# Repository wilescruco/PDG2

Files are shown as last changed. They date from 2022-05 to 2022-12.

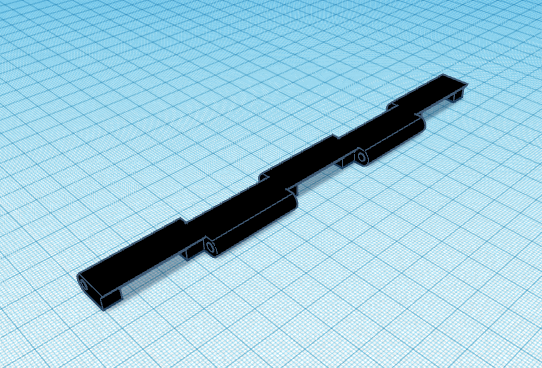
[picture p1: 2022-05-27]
DISEÑOS DE CONSTRUCCIÓN/Diseños de las Piezas impresas en 3D Banda/Pieza Banda.png

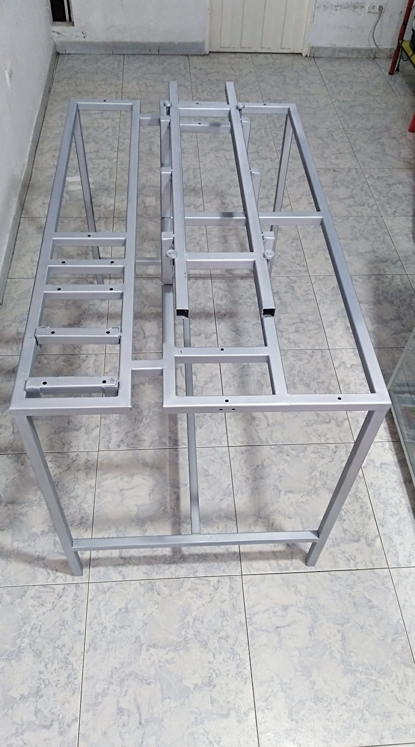
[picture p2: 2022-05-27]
DISEÑOS DE CONSTRUCCIÓN/FOTOS MESA BANDA TRANSPORTADORA/2. ESTRUCTURA METALICA.jpg

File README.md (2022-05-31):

# PDG2
BANCO PARA PRÁCTICAS DE AUTOMATIZACIÓN INDUSTRIAL, CONTROL AUTOMÁTICO DE UNA BANDA TRANSPORTADORA MEDIANTE UN VARIADOR DE FRECUENCIA CON PLC

Completa

Mecanismo interno

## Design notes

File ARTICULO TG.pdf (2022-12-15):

# BANCO PARA PRÁCTICAS DE AUTOMATIZACIÓN INDUSTRIAL, CONTROL AUTOMÁTICO DE UNA BANDA TRANSPORTADORA MEDIANTE UN VARIADOR DE FRECUENCIA CON PLC

Wilson Sneider Cruces, Paola Andrea Ovalle

Fundación Universitaria Unisangil

wilsoncruces@unisangil.edu.co

paolaovalle@unisangil.edu.co

Resumen— El siguiente articulo contiene el desarrollo del diseño e implementación de un banco para prácticas de automatización aplicando control automático a una banda transportadora mediante un variador de frecuencia controlado por PLC, este proyecto además de su estructura física, cuenta con guías de laboratorio, manual de usuario y planos eléctricos que le permitirá a los estudiantes de la Fundación Universitaria Unisangil sede Yopal, interactuar y poner en práctica los conocimientos teóricos adquiridos en las diferentes áreas de la ingeniería tales como instrumentación industrial, maquinas rotativas, programación, control y automatización de procesos, mediante el desarrollo de prácticas de laboratorio.

Abstrac— The next document contains the development of the design and implementation of a bench for automation practices applying automatic control to a conveyor belt through a frequency inverter controlled by PLC, this project, in addition to its physical structure, has laboratory guides, a user manual and electrical plans that will allow the students of the Yopal Unisangil University Foundation to interact and put into practice the theoretical knowledge acquired in the different areas of engineering such as industrial instrumentation, rotating machines, programming, control and process automation, through the development of laboratory practices.

I. INTRODUCCIÓN
GSL industrias define la automatización industrial como el uso de sistemas computarizados, electromecánicos, electroneumáticos y electrohidráulicos para fines industriales. Dentro de las ramas de ingeniería, es uno de los procesos más completos y transversales a diferentes actividades industriales a nivel nacional. [1]

El presente articulo da a conocer el proceso de diseño e implementación de banco para prácticas de automatización aplicando control automático a una banda transportadora mediante un variador de frecuencia controlado a través de un PLC, con el objetivo de que en un futuro permita a estudiantes de carreras universitarias afines, desarrollar sus prácticas en las áreas de instrumentación industrial, maquinas rotativas, programación, control y automatización de procesos, quedará disponible para que los profesionales en formación puedan valerse de él para afianzar sus conocimientos, además, servirá de base para futuras mejoras o innovaciones.

II. PLANTEAMIENTO DEL PROBLEMA

En Colombia según datos de Asocoldep la ingeniería Electrónica está dentro de las carreras mejor pagadas y con mayor demanda en vinculación laboral con un promedio del 84.4%. Convirtiéndola en una buena opción de formación profesional. La accesibilidad a estas carreras universitarias es relativamente fácil, además hay un número considerable de universidades que ofrecen diferentes programas profesionales de ingenierías, estando al alcance de cualquier joven con aspiraciones de aprendizaje en estas áreas. Dentro de estas entidades de formación existe una problemática, que interfiere en el proceso de formación de estos profesionales y se trata de la falta de espacios adecuados y laboratorios que les permita a los ingenieros electrónicos en
formación | desarrollar | sus | conocimientos, | aplicarlos | y
relacionarlos en los campos de la instrumentación industrial,
electrónica | de | potencia, | diseño | electrónico, | control | y
automatización. [2]

La Fundación Universitaria de San Gil UNISANGIL sede Yopal que cuenta con un amplio grupo de jóvenes con grandes inspiraciones de aprendizaje, encaminados en un proceso de formación en diferentes facultades de las ingenierías, una de ellas la ingeniería electrónica. Esta ingeniería es una carrera profesional con bastante exigencia como cualquier otra, su etapa de teoría como la práctica, son muy importantes a la hora de pensar en ser un excelente profesional. Teniendo en cuenta lo anterior la sede UNISANGIL Yopal viene trabajando en fortalecer sus espacios de laboratorio de tal manera que les brinde a sus estudiantes un ambiente de aprendizaje apropiado dotado con recursos que permita realizar las prácticas de laboratorio, espacio esencial para el proceso de formación profesional.

III. FORMULACIÓN DEL PROBLEMA.

¿ La construcción de un banco para prácticas de automatización industrial, control automático de una banda transportadora mediante un variador de frecuencia con PLC, ayudará a los estudiantes de ingeniería electrónica a mejorar sus habilidades en el desarrollo de prácticas de programación de PLC y automatización?

IV. JUSTIFICACIÓN.

Una de las principales áreas de desempeño de un ingeniero electrónico es la automatización y control de procesos; los procesos automatizados en la actualidad tienen una alta demanda ya que el diseño de estos sistemas van enfocados al mejoramiento y optimización del mismo, teniendo en cuenta lo anterior, se considera de vital importancia que la Fundación Universitaria de San Gil Unisangil cuente con espacios de laboratorios adecuados que les permita a los ingenieros en formación interactuar con equipos, sistemas y tecnologías implementadas en áreas de Instrumentación, control y automatización, tales como el controlador lógico programable.

Pensando en la calidad de formación del ingeniero electrónico, la Fundación Universitaria Unisangil sede Yopal ha venido mejorando los espacios laboratorio de electrónica, hasta el momento varios estudiantes que están finalizando su proceso de formación, como trabajo de grado, han desarrollado e implementado diferentes bancos de prácticas; con el fin de seguir contribuyendo con la adecuación y equipamiento de esta área tan importante el en proceso de formación de los ingenieros electrónicos, nace la idea de diseñar un banco para prácticas de automatización industrial, en este caso, el control automático de una banda transportadora mediante un variador de frecuencia con PLC. Este nuevo banco para practicas quedará al servicio del laboratorio de la universidad y para uso de todos los estudiantes del programa de ingeniería electrónica, de esta manera la Fundación Universitaria de San Gil UNISANGIL mejorará tanto su laboratorio como la calidad de formación que ofrece a sus profesionales.

V. OBJETIVOS
A. Objetivo general.

Diseñar e implementar un banco para prácticas de automatización aplicando control automático a una banda transportadora mediante un variador de frecuencia con PLC.

B. Objetivos específicos
- Desarrollar la plataforma de trabajo de la banda transportadora.
- Diseñar y realizar la estructura del banco de prácticas, donde se integre la banda transportadora y el motor junto con su control automático
- Desarrollar el programa para el controlador lógico programable que permita la automatización del proceso mediante el variador de frecuencia.
- Realizar pruebas de funcionalidad del sistema para verificar su correcto funcionamiento y de esta manera alcanzar el objetivo principal del proyecto.
- Diseñar cuatro guías de laboratorio que les permita a los estudiantes interactuar con el banco de prácticas y conocer cada uno de los sistemas que lo componen.

VI. ESTADO DEL ARTE.

En la fundación universitaria Unisangil sede Yopal, los Ingenieros en formación le han apostado a contribuir con el equipamiento de los espacios de laboratorio de la ingeniería, con el desarrollo e implementación de bancos para prácticas de neumática, electro neumático, modulo variador de frecuencia, banco de procesos industriales, entre otros, estos proyectos, además de permitirle a los ingenieros en formación aplicar sus conocimientos con ejecución de estos, también contribuyen a la formación de todos los estudiantes de ingeniería electrónica de la facultad, creando espacios apropiados para fomentar sus conocimientos mediante el desarrollo practico de guías de laboratorio aplicativas a los bancos implementados en el laboratorio; en el años 2016 fue desarrollado por dos estudiantes de ingeniería electrónica como proyecto de grado el diseño e implementación de un módulo didáctico para el control de presión, temperatura y nivel dirigido hacia las áreas de instrumentación industrial, control y automatización del programa de ingeniería electrónica de UNISANGIL, en la siguiente figura se puede observar el banco de procesos industriales implementado.

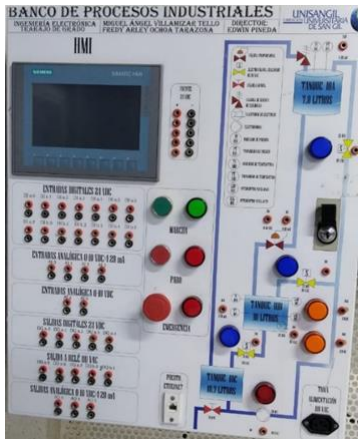
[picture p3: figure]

IMAG 1: Modulo didáctico

En la Universidad Antonio Nariño de Bogotá, dos estudiantes de Ingeniería Electromecánica desarrollaron como proyecto de grado un banco didáctico, se trata del diseño de un banco de prácticas donde se integra un controlador lógico programable, un VFD con motor eléctrico trifásico y fue implementado en el laboratorio de automatización de la facultad. EL principio de funcionamiento de este banco de prácticas se basa en que la carga variable del motor está condicionada por el cambio de temperatura de un fluido en función de su viscosidad, de tal manera el sistema realiza la supervisión de la temperatura del fluido por medio del PLC. Durante el proceso de diseño los estudiantes realizaron el análisis de diferentes variables eléctricas presentes en la operación del banco con el fin de identificar los parámetros a ajustar en el variador de velocidad para controlar las RPM del motor. Con la implementación de este proyecto se buscó incentivar el desarrollo de prácticas orientadas al uso de equipos de programación industrial con el objetivo principal de afianzar conceptos y adquirir nuevas destrezas; teniendo en cuenta la aplicación de este banco de prácticas, está diseñado para operar con un motor trifásico con potencia máxima 0,37 kW a una tensión de 220 V ac, el sistema de control y monitoreo integrado por PLC, variador, sensores y pulsadores se encuentran instalados en una estructura con dimensiones 1,20 metros de ancho, 60 cm de alto y con profundidad de 30 cm además, se realizan los manuales de ensamblaje en sitio de todos los componentes del banco de prácticas e instructivo de puesta en servicio, también los correspondientes archivos de programación para la parametrización del controlador lógico programable y el variador de velocidad.[3]
IMAG 2: Banco de prácticas con PLC.

Por su parte, como lo refiere Buitrago & Rodríguez , en la universidad Santo Tomas estos dos estudiantes de la facultad de ingeniería mecánica desarrollaron como proyecto de grado un material didáctico para el espacio académico de la facultad aplicado al área de automatización e instrumentación, es este caso se trata de la elaboración de dos guías de prácticas donde se diseña la automatización de dos procesos industriales diferentes, los estudiantes realizan la simulación del proceso automático de empaquetamiento de productos , el control automático de calidad y el desarrollo de la programación del controlador lógico programable para la automatización de los dos procesos anteriormente nombrados.[4]

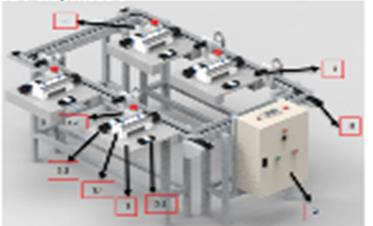
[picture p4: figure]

IMAG 3: Material didáctico para prácticas.

De la misma manera, en la Universidad Autónoma de Zacatecas Francisco García Salinas, dos estudiantes presentaron como tesis de licenciatura un control de velocidad de una banda transportadora para la clasificación de objetos. Este proyecto se llevó a cabo a partir de la construcción de un prototipo de una banda transportadora, impulsada por un motor de corriente directa a 24 V, el control de velocidad de la banda transportadora está condicionada con la implementación de diferentes sensores y un código de programación para el controlador lógico programable PLC S7-200 de SIEMENS.[5]

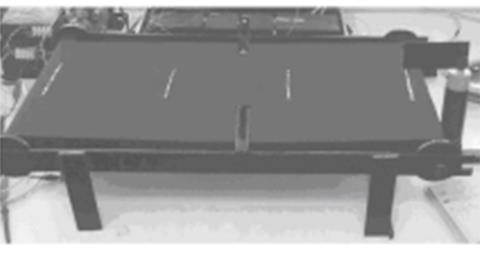
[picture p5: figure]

IMAG 4: Prototipo banda transportadora.

Finalmente, como lo realizó Batioja en su trabajo de titulación, sobre la Automatización de un sistema de bandas transportadoras para el abastecimiento de trozas en Contrachapados de Esmeraldas S.A – Codesa, el proyecto consistió en realizar la automatización del sistema de bandas transportadoras mediante el uso de un PLC Siemens 1200, sensores mecánicos, fotoeléctricos, dispositivos de maniobra, operación, protección y actuadores rotativos y lineales. Para realizar operaciones de supervisión, alertas tempranas de fallas y control de unas cuantas variables se incluirá un interfaz humano máquina HMI. La fábrica Contrachapado de Esmeraldas S.A – Codesa opera principalmente con un suministro de energía de 220/380 VAC, por lo cual los equipos, dispositivos y actuadores deben considerar esta especificación eléctrica. [6]

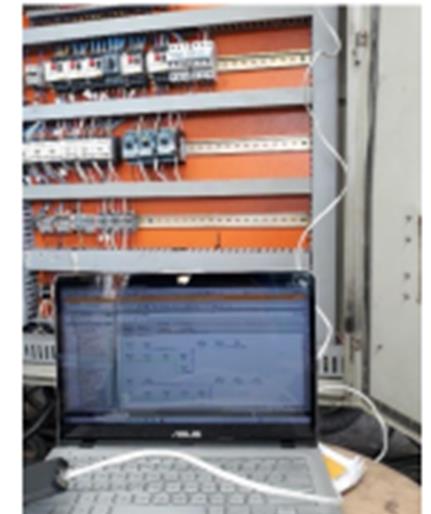
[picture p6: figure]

IMAG 5. Sistema automatizado

VII. DESARROLLO LA PLATAFORMA TRABAJO DE LA BANDA TRANSPORTADORA

A. Diseño.

Inicialmente, se realiza el diseño de la plataforma de trabajo de la banda transportadora a mano alzada, teniendo en cuenta que las dimensiones sean proporcional las medidas del banco de prácticas y el espacio del laboratorio donde será instalado finalmente, sus dimensiones son de 1 metro de largo, 17,5 centímetros de ancho y 10 cm de alto , Con ayuda de la herramienta informática Thinkercad se monta el diseño verificando una presentación adecuada estéticamente y funcional, en la siguiente figura se puede

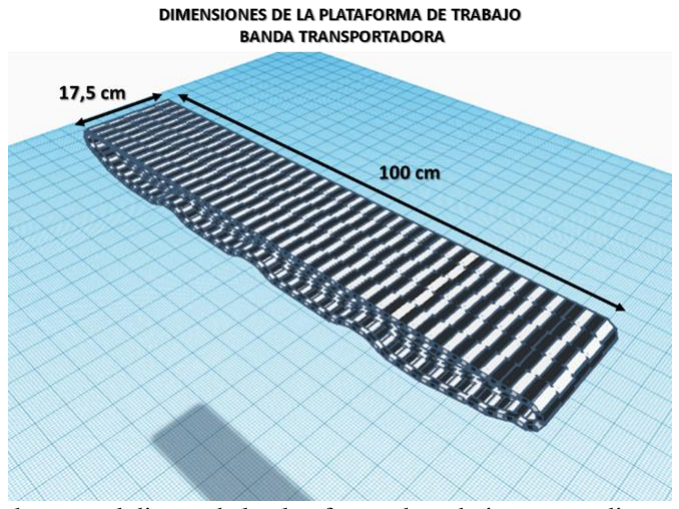
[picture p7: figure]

observar el diseño de la plataforma de trabajo con sus dimensiones. | IMAG 6. Diseño de plataforma de trabajo.

Así mismo, se realiza el diseño de cada uno de los componentes de la banda transportadora, entre ellos el mecanismo de empuje, el rodillo accionado o impulsado, rodamientos, el engranaje y la estructura de física del sistema, su diseño también fue realizado con ayuda de la herramienta Thinkercad, en la siguiente figura se muestra el diseño de los componentes de la banda transportadora.

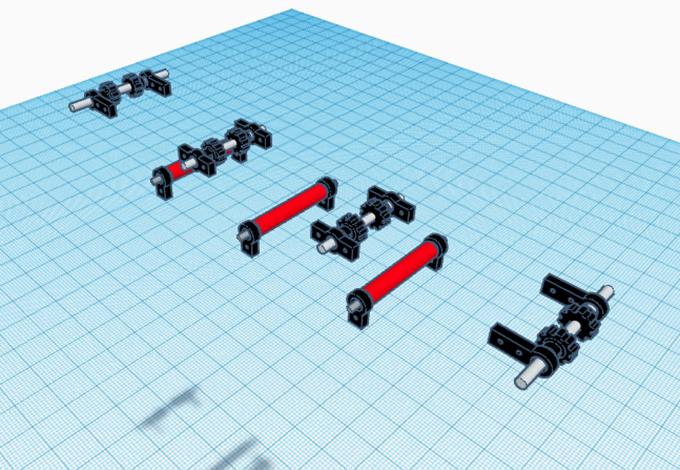
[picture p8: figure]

IMAG 7: Diseño de componentes.

Finalmente, ya con el diseño de la banda transportadora y cada una de sus partes, se realiza un montaje en la herramienta Thinkercad donde se integra cada uno de los componentes, se realiza la presentación y se valida que el diseño de la plataforma está de acuerdo al fin deseado, en la siguiente figura se muestra el diseño final de la plataforma de trabajo de la banda transportadora.

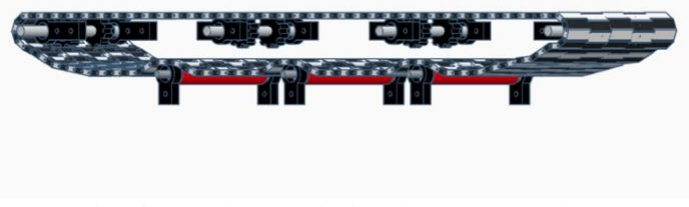
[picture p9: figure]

IMAG 8. Plataforma de trabajo banda transportadora.

B. Implementación.

Buscando minimizar los costos del proyecto y garantizando la calidad de los componentes, se planeó realizar la mayoría de las partes de la plataforma de trabajo, en impresión 3D con filamento PLA, se imprimieron 8 engranajes los cuales son los elementos encargados de permitir el giro o mecanismo de desplazamiento de la banda, estos engranajes irán montados con la distribución de 2 por cada eje; el diseño de la banda o faja tiene una dimensión de 2,10 metros de larga por 17.5 centímetros de ancha, para construir la banda con esas dimensiones fue necesario la impresión en 3D de 154 piezas modulares, estas piezas modulares fueron diseñadas con unas pestañas las cuales encajan con los dientes del engranaje, el objetivo de este sistema es movilizar la banda en paralelo al giro del engranaje; para el soporte de los ejes se diseñaron 4 soportes intermedio y 4 soportes para los extremos, estos elementos serán los encargados de fijar y asegurar cada uno de los 4 ejes del sistema de desplazamiento de la banda, en la siguiente figura se muestra las partes de la plataforma de trabajo impresas en dimensión 3D.

Dentro del diseño del mecanismo de giro o desplazamiento de la banda se contempla el uso de 4 ejes en material de acero plata, este material se considera adecuado ya que es resistente y de buena apariencia física, cada eje es de 19 cm aproximadamente, uno de estos ejes recibe el nombre de mecanismo de empuje el cual será accionado por reductor de giro 10:1 conectado al motor de 0.4 Hp. En cada eje ira instalado 2 engranajes; en el diseño del mecanismo de desplazamiento de la plataforma de trabajo para la banda transportadora se ve necesario incluir un sistema de rodamientos, se emplean un total de 12 rodamientos 608 2RS distribuidos de la siguiente manera, 4 rodamientos soldados a la estructura metálica los cuales influyen en la alienación de la banda, 8 instalados en los ejes del sistema de desplazamiento, en la siguiente figura se muestra el tipo de eje y rodamiento usado.

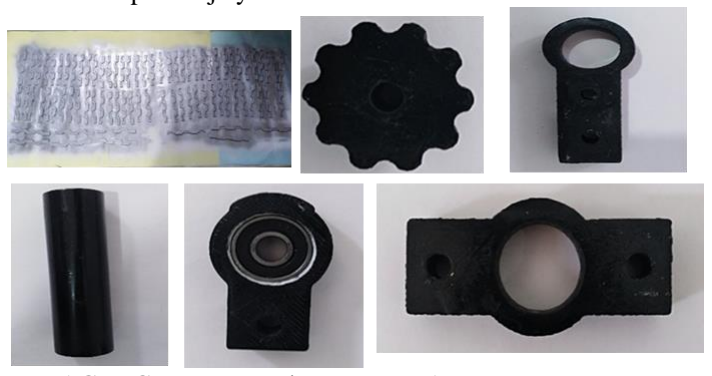
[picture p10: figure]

IMAG 9: Componentes impresos PLA.

Las 154 piezas modulares junto con cada uno de los componentes requeridos para la plataforma de trabajo entre ellos, 8 engranajes, 3 rodillos, 4 soportes intermedio del eje, 4 soporte de extremo del eje, 6 ejes de soporte para los rodillos, se construyen de manera satisfactoria según el diseño a base de filamento PLA impreso en dimensión 3D, las piezas modulares se integraron con radios de bicicleta ya que es un material resistente y apropiado para la finalidad de su uso.

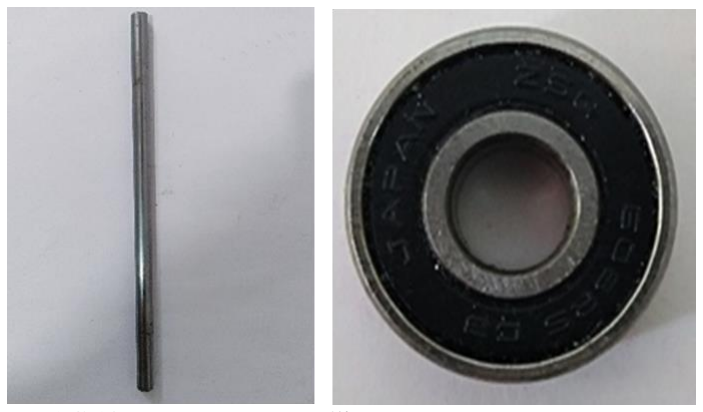
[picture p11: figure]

IMAG 10: componentes metálicos.

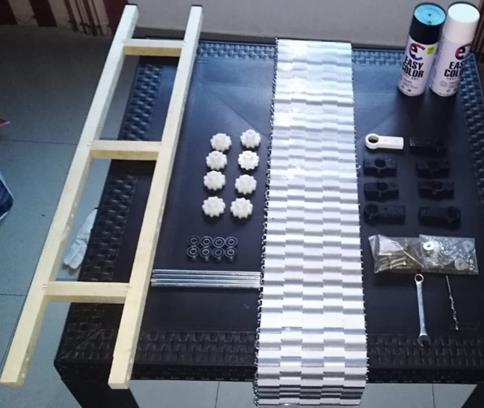
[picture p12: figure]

IMAG 11: componentes banda transportadora.

Con el fin de validar la resistencia de cada uno de los componentes impresos en PLA, el correcto funcionamiento y realizar una presentación provisional, se construye una estructura para la plataforma de trabajo de la banda transportadora en material amaderado, su construcción se realiza teniendo en cuenta el diseño inicial y las dimensiones contempladas, tal como se muestra en la siguiente figura.

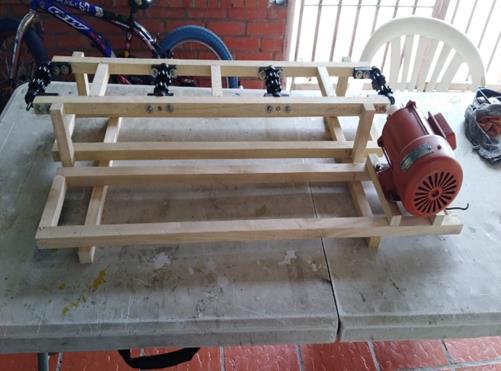
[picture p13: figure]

IMAG 12: Estructura en madera.

Se integra cada uno de los componentes armando la plataforma de trabajo sobre la estructura de madera, se valida resistencia del material, correcto funcionamiento y presentación adecuado de acuerdo al diseño inicial, lo anterior se realizó acondicionado un motor trifásico de 0.4 Hp al rodillo de empuje de la banda; durante el desarrollo de esta prueba de funcionamiento se evidencia la necesidad de implementar un reductor de velocidad con el fin de aumentar la frecuencia de operación del motor ya que la frecuencia actual oscila entre 0 a 20 Hz, adicionalmente, se observa que en la parte inferior de la banda se forma un seno accionando fricción con la estructura, por tal motivo es necesario implementar unos rodillos adicionales para mantener la firmeza de la banda y así eliminar la fricción observada, se diseñan 3 rodillos y se construyen a base de filamento PLA impreso en dimensión 3D, adicionalmente para garantizar el mecanismo de giro de los rodillos se implementan 6 rodamientos 608 2RS más, en la siguiente figura se observa la presentación de la plataforma de trabajo acoplado al mecanismo de giro de la banda.

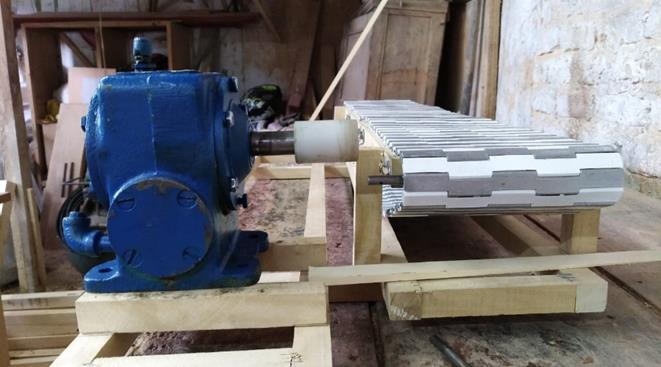
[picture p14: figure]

IMAG 13: Conexión banda mecanismo de giro.

Como proceso final para alcanzar el primer objetivo planteado y luego de validar el funcionamiento correcto de la plataforma de trabajo para la banda transportadora, se procede a realizar el montaje de la estructura final en material metálico, integrando cada uno de los componentes fabricados en filamento PLA impreso en 3D anteriormente relacionados, los 18 rodamientos 608 2RS y los 4 ejes de 19 cm aprox, como se muestra en la siguiente figura.

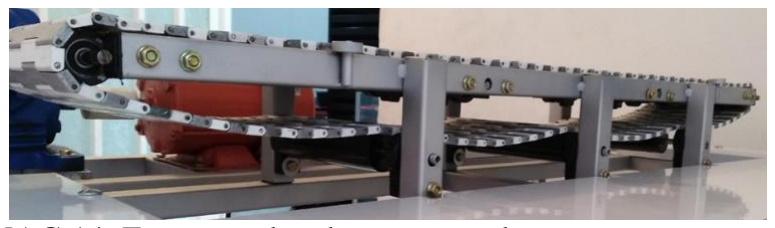
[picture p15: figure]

IMAG 14: Estructura banda transportadora.

VIII. DISEÑO E IMPLEMENTACIÓN DE LA ESTRUCTURA DEL BANCO DE PRÁCTICAS.
A. Diseño.

Teniendo en cuenta la importancia de contar con un escenario cómodo, adaptable al espacio del laboratorio de electrónica de la facultad y basado en los tamaños de los bancos de prácticas existentes, se diseña una estructura para el banco de prácticas con dimensiones de 1,20 metros de largo y un ancho de 71,5 centímetros, basado en otro aspecto y no menos importante como son los espacios de trabajo adecuados ergonómicamente, este banco de prácticas se diseña con una altura de 85 centímetros, apostando a la comodidad del usuario; La estructura del banco de prácticas de automatización está diseñada de tal manera que permite la instalación de manera estética y adecuación de cada uno de los equipos que lo componen tales como el motor, reductor de giro y la plataforma de trabajo de la banda transportadora.

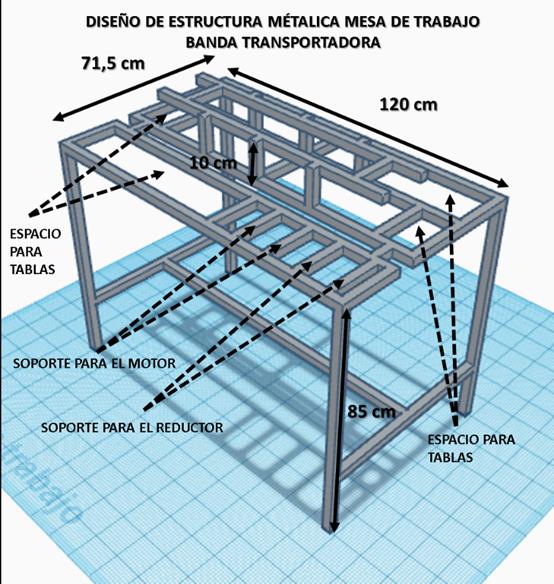
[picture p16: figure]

IMAG 15: Diseño banco de prácticas.

Adicionalmente el diseño de la estructura del banco cuenta con un espacio libre el cual puede ser usado por los estudiantes como escritorio o en su defecto, para integrar a bancos de prácticas disponibles en la facultad o acondicionar a nuevas ideas para el desarrollo de proyectos, el diseño de este espacio tiene las dimensiones mostradas en la siguiente Figura.

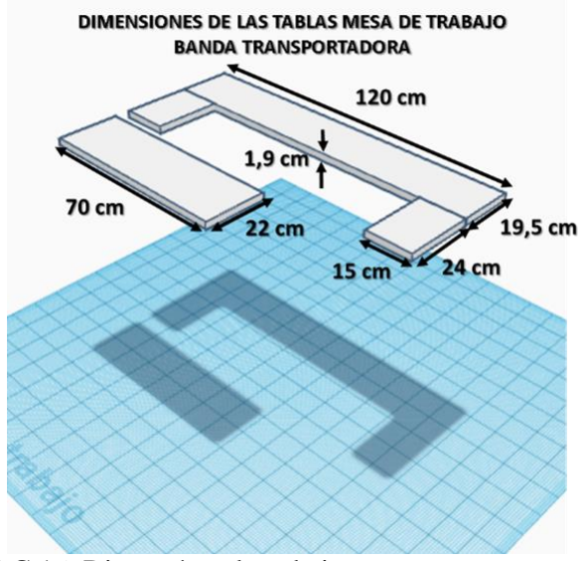
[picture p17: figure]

IMAG 16: Diseño área de trabajo.

El banco para prácticas de automatización industrial, también cuenta con el diseño de una estructura donde se instala el sistema de control del proceso, las dimensiones de esta estructura se definen teniendo en cuenta el espacio requerido para la instalación de cada uno del componente del sistema de control tales como el controlador lógico programable, el VSD, switch, pantalla HMI, la fuente regulador, accesorios y la distribución de entradas y salidas, el tamaño diseñado también es proporcional a las dimensiones del banco de prácticas teniendo en cuenta el espacio para su instalación; en la siguiente figura se muestra el diseño de la estructura con dimensiones.

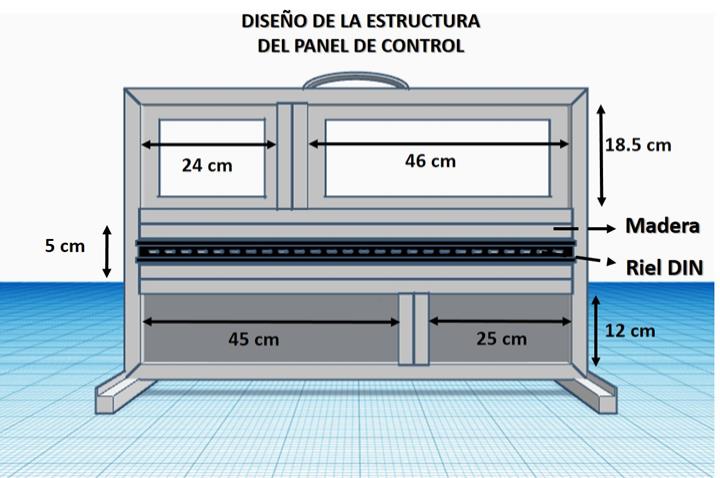
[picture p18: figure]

IMAG 17: Diseño estructura panel de control.

Para las líneas de alimentación del banco de prácticas, se diseña un plano eléctrico con la distribución de la alimentación adecuada para cada equipo, se implementó un interruptor tripolar el cual alimenta en variador, las 3 fases de alimentación del motor esta derivada desde el variador, el panel de control esta alimentado de una de las fases del motor por medio de un interruptor de 10 A, este interruptor es el general del panel de control, el cual también alimenta la fuente, la fuente de voltaje tiene 2 salidas de 24 v, una de ellas conectada a un interruptor de 6 A, la cual controla 24 v y la línea a tierra del lado dereche del panel de control, la otra salida esta conecta a un interruptor de 3 A, de punto de conexión se deriva la alimentación para los 5 fusibles implementados para PLC, switch,HMI, entradas digitales y salidas digitales.

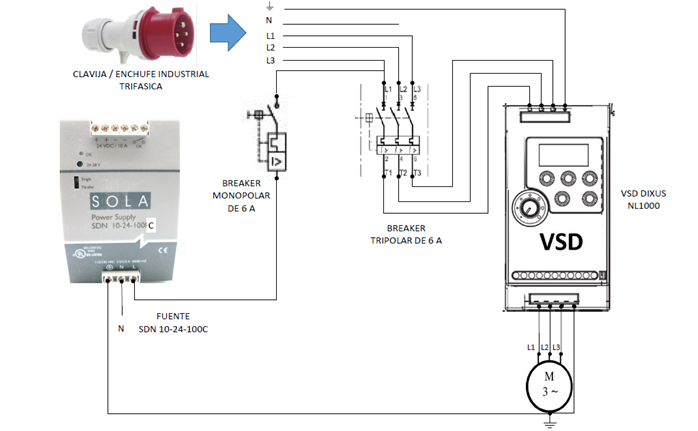
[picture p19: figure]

IMAG 18: Plano de distribución eléctrica AC.

B. Equipos.

Dentro de los equipos que componen el banco para prácticas de automatización industrial, control automático de una banda transportadora mediante un variador de frecuencia con PLC tenemos

Motor eléctrico: esta máquina rotativa es la encargada de convertir la energía eléctrica en energía mecánica, para el desarrollo de este proyecto se implementa un motor trifásico asíncrono o de inducción de 0.4 Hp, marca SIEMENS, con serie 1LA3, frecuencia de 60 Hz, velocidad nominal de 1640 rpm, la selección del motor se realiza teniendo en cuenta el peso de la banda transportadora diseñada ya que este es el mecanismo de giro el banco de prácticas

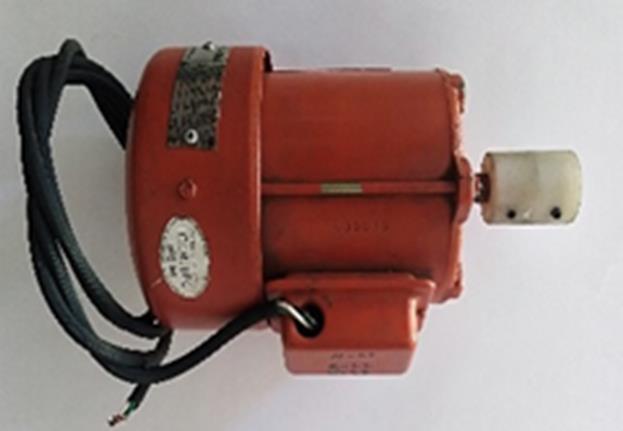
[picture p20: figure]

IMAG 19: Motor Trifásico.

Reductor de velocidad: en la prueba de funcionalidad de la plataforma de trabajo se identificó la necesidad de implementar un reductor de giro con el fin de mejorar la frecuencia de operación del motor, sin el reductor de velocidad la banda operaria a una velocidad muy alta aproximada a la velocidad nominal del motor a 60 Hz, se realiza la adaptación de un reductor de velocidad 10:1, para conectar el motor con el reductor se requirió 1 acople el cual fue fabricado en material nylon.

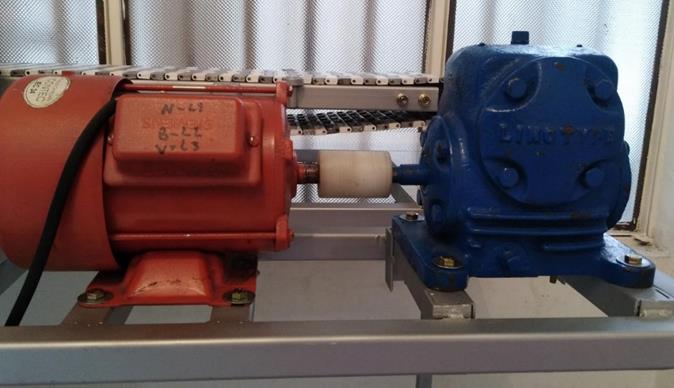
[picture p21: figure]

IMAG 20: Acoplamiento motor reductor.

Para control automático de una banda transportadora mediante un variador de frecuencia con PLC, se utilizó VSD NL1000 este variador de frecuencia se escogió teniendo en cuenta su bajo costo comparado con otros en el mercado, además, aunque en este banco de prácticas se usan solo las entradas digitales este VSD tiene otras formas de operación las cuales podrán ser usadas en futuras innovaciones del proyecto, otro aspecto tenido en cuenta es el tamaño, fácil instalación y cableado.

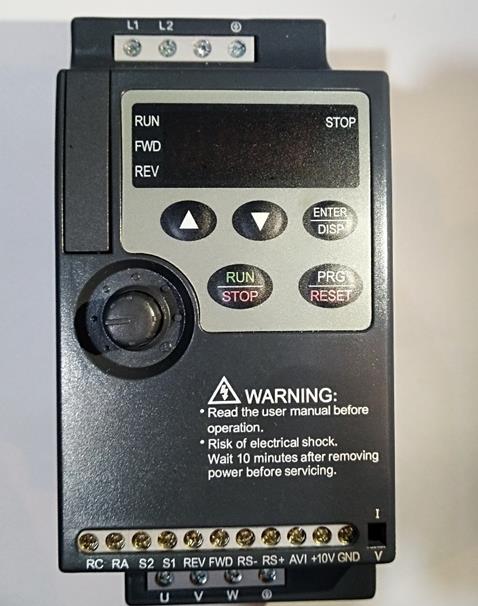
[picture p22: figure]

IMAG 21: VFD.

El sistema de control de la banda transportadora además del VSD está compuesto por un módulo de control disponible en el laboratorio de electrónica de la Universidad, este módulo consta de una pantalla HMI SIMATIC HMI, KTP700 Basic, un Switch Siemens SCALANCE XB005, un PLC Siemens S7-1200 y una fuente de alimentación SDN 10-24-100C, cada uno de estos equipos son instalados en la estructura diseñada para el panel de control del banco.

C. Implementación.

Teniendo en cuenta el diseño y medidas de la estructura del banco para prácticas, con ayuda de un ornamentador se realiza el corte de cada una de las partes de la estructura, se unen con material soldado apropiada para el material, las terminación y uniones son pulidas cuidadosamente para evitar bordes filosos o con potencial de daño para los usuarios, finalmente con el objetivo una mejor presentación estética de la estructura y conservación del material metálico se le aplico base anticorrosiva y una capa de laca color aluminio. En la siguiente figura se muestra el resultado final la estructura del banco de prácticas construido.

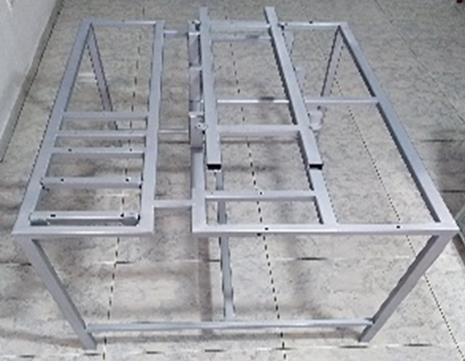
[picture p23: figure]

IMAG 22: Estructura metálica.

La estructura para el sistema de control se construye a partir del diseño inicial, esta estructura es elaborada en material aluminio, algunas partes en materia acero inoxidable y acrílico, en esta estructura se acondiciona el PLC/HMI, el variador de frecuencia VSD, la fuente reguladora, el switch y cada uno de los accesorios requeridos para la adecuación de las señales de entradas y salidas del módulo de control, adicionalmente, cuenta con un espacio para la identificación del banco, allí se realiza la instalación de una placa que fue diseñada e impresa con el número y nombre del banco como se puede evidenciar en la siguiente figura.

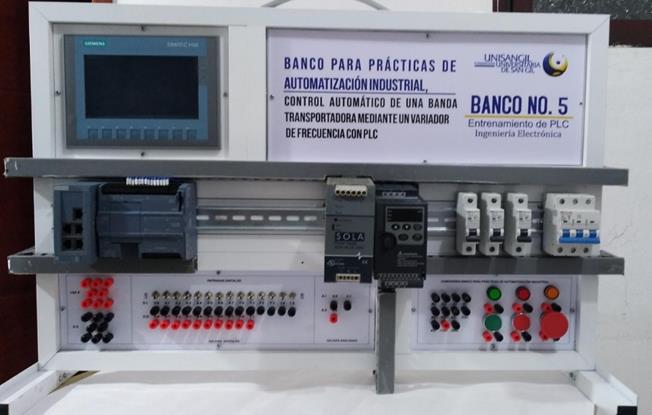
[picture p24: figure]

IMAG 23: Panel de control.

Como resultado final se obtiene la estructura del banco de prácticas con medidas acordes y buena presentación física, se integra cada uno de los componentes del banco entre ellos la plataforma de trabajo de la banda transportadora, el motor con reductor de giro y el módulo de control, se realiza la instalación y adecuación de los cables de conexión para las diferentes señales del sistema, cada uno de los dispositivos fueron conectados, finalmente se cumple con el segundo objetivo general del proyecto.

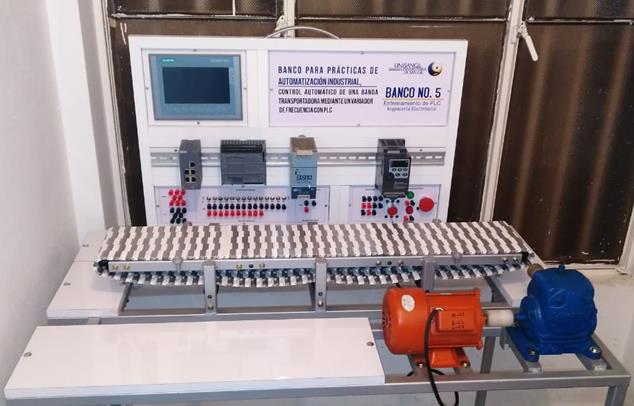
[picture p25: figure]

IMAG 24: Banco para prácticas.

IX. DESARROLLO EL PROGRAMA PARA EL CONTROLADOR LÓGICO PROGRAMABLE

A. Diseño.

El programa planteado a continuación simula el control de una banda transportadora mediante un variador de frecuencia (VSD) siendo accionado por pulsadores para el inicio, parada, cambio de giro y una parada de emergencia, todo comandado desde un controlador lógico programable (PLC). Que toma como entrada las señales de los pulsadores y entrega una señal de control para la operación del VSD.

B. Implementación.

En este segmento 1: se realiza el enclavamiento principal de la variable “SISTEMA” la cual es accionada con el pulsador de color verde “START” permitiendo que la banda transportadora quede habilitada para su funcionamiento y en espera de una nueva orden para iniciar el desplazamiento a la derecha o la izquierda, a su vez encenderá la luz piloto color verde “LuzPilotoVerde”. Cuando se oprime el pulsador de color rojo “STOP” dejará de funcionar el SISTEMA. Por otra parte, al accionar el botón de parada de emergencia “EMERGENCYSTOP” también dejará de operar el sistema.

IMAG 25: Segmento 1.

En este segmento 2: se realiza la configuración para el inicio del desplazamiento de la banda transportadora hacia el lado derecho. Una vez este habilitado el “SISTEMA” y después de ser accionado un pulsador “IFWD” conectado a la entrada digital %I0.3 se activará un pulso “FWD” que será conectado a la entrada digital del VSD permitiendo el giro de la banda transportadora hacia el lado derecho. También se garantiza que mientras no haya otro pulso solo girará hacia ese lado.

IMAG 26. Segmento 2.

En este segmento 3: se realiza la configuración para el inicio del desplazamiento de la banda transportadora hacia el lado izquierdo. Una vez este habilitado el “SISTEMA” y después de ser accionado un pulsador “IREV” conectado a la entrada digital %I0.4 se activará un pulso “REV” que será conectado a la entrada digital del VSD permitiendo el giro de la banda transportadora hacia el lado izquierdo. También se garantiza que mientras no haya otro pulso solo girará hacia ese lado.

IMAG 27. Segmento 3.

En este segmento 4: Se realiza la configuración para qué cuando esté desactivado el “SISTEMA” no se permita el desplazamiento de la banda para ninguno de los dos lados (derecha e izquierda). La desactivación se logra accionado el pulsador rojo “STOP” o el botón de para de emergencia “EMERGENCYSTOP”.

IMAG 28. Segmento 4.

En este segmento 5: Se realiza la configuración para qué cuando se accione el pulsador rojo “STOP” se detenga la banda transportadora de manera segura con una desaceleración controlada y se encienda la luz piloto roja “LuzPilotoRoja” durante 5 segundos. Después de este tiempo se apagará la luz piloto roja.

IMAG 29. Segmento 25.

En este segmento 6: Se realiza la configuración para qué cuando
se | accione | el | botón | de | parada | de | emergencia
“EMERGENCYSTOP” se detenga la banda transportadora de manera segura con una desaceleración controlada y se encienda la luz piloto roja “LuzPilotoNaranja” durante el tiempo que dure accionado el botón.

IMAG 30. Segmento 6.

Se debe realizar la configuración previa básica del variador Nietz NL1000-02R2G2 para poder utilizarlo con un motor asíncrono trifásico de 0.4 HP. La configuración se realizará en tres etapas:

Parámetros básicos del motor.
Selección del método de mando.
Tiempos de arranque y paro, frecuencias máxima y mínima.
X. PRUEBAS DE FUNCIONAMIENTO DEL BANCO.

Las pruebas de funcionamiento del sistema se dividen en tres secciones; en la primera sección se realizaron las pruebas funcionales de la estructura física del sistema, en la segunda sección se realizan las pruebas de operatividad del banco y la tercera sección se realizó pruebas funcionales del sistema de control del banco para prácticas de automatización industrial.

En las pruebas funcionales de la estructura física, se validó el funcionamiento adecuado de cada uno del componente, en las pruebas del sistema de giro se evidencio la necesidad de implementar un reductor de velocidad; en la prueba de funcionalidad de la banda transportadora se evidencia la necesidad de implementar otros soportes para facilitar el desplazamiento, se hicieron las modificaciones obteniendo finalmente un banco de prácticas para automatización acorde a lo planteado.

En las pruebas de operatividad del banco, se realiza prueba de continuidad de cada una de las conexiones, se realiza mediciones de tensión, se verifica el voltaje: de alimentación de la fuente (120 VAC) voltaje que entrega la fuente (24 vdc). Voltaje de entrada y salida del VSD, se realiza prueba de giro del motor, medición de intensidad de corriente en cada fase del motor, se verifica que corresponda a la placa de características del motor; Posteriormente se realiza un programa básico en donde se pruebe cada entrada y salida digital del PLC. Y por último se corre el programa general que se realizó para controlar la banda transportadora mediante un VSD siendo accionado por salidas digitales del PLC.

Finalmente, en las pruebas funcionales del sistema se verifica el control automático de la banda transportadora mediante un variador de frecuencia con PLC, implementando el desarrollo de la guía de laboratorio N° 4 del proyecto “CONTADOR DE CANASTAS CON UN DETERMINADO NUMERO DE PRODUCTOS”, registrando los siguientes resultados funcionales.

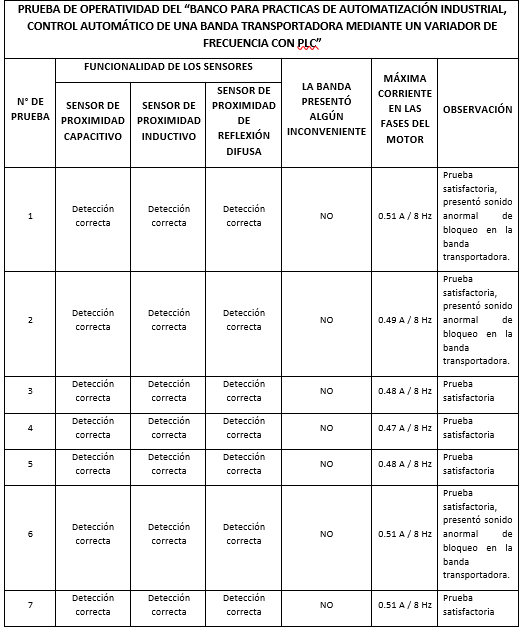
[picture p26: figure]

IMAG 31. Resultados prueba funcionales.

IMAG 31. Resultados prueba funcionales.

XI. CONCLUSIONES.

La estructura de trabajo de la banda transportadora, se desarrolló de manera satisfactoria con diseños adecuados al espacio donde se instalará finalmente, esta plataforma de trabajo fue fabrica en filamento PLA y sometida a pruebas de funcionamiento con el objetivo de garantizar su calidad.
Se diseño e implemento la estructura para el banco de prácticas con dimensiones acordes al espacio del laboratorio donde será instalado, esta plataforma de trabajo esta creada con espacios adecuado para la instalación de cada uno de los equipos que la compone, así como también cuenta con un espacio libre, el cual podrá ser usado para desarrollar nuevos proyectos e ideas innovadoras de los estudiantes en formación.

El programa para control de velocidad de la banda trasportadora mediante el variador de frecuencia LN 1000 desarrollo en el software TIA Portal, el código del programa está compuesto por 6 segmentos, cada uno de ellos con diferentes funciones en el sistema del control automático de la banda transportadora.

En las diferentes etapas de construcción del banco para prácticas de automatización se realizaron diferentes pruebas, validando el funcionamiento correcto de cada componente del proyecto, por medio de ellas se identificaron oportunidades de mejora que conllevaron al logro de cada uno de los objetivos específicos y como tal el objetivo general.

Se diseñaron cuatro guías de laboratorio con aplicación al banco de prácticas, la finalidad de estas guías es incentivar al uso de este banco para prácticas de automatización de tal manera que los ingenieros en formación interactúen con los equipos, pongan en prácticas los conocimientos teóricos vistos en su proceso de formación en el área de automatización y control adquiriendo bases fundamentales, conocimiento y competencias en el área.

Finalmente, al finalizar este proyecto e implementarlo, se está contribuyendo al mejoramiento del área de laboratorio de la Universidad y así mismo, al fortalecimiento de habilidades y competencias de los ingenieros electrónicos y carreras afines.

REFERENCIAS

[1] GSL INDUSTRIAS. Que es la automatización industrial [Artículo en línea]. 18
de | noviembre | de | 2020. | Disponible | en
https://industriasgsl.com/blogs/automatizacion/que-es-la-automatizacion-industrial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,y %20electrohidr%C3%A1ulicos%20para%20fines%20industriales.
[2] ASOCOLDEP. ¿Cuáles son las carreras universitarias más demandadas y mejor pagadas en Colombia? [En línea]. 2020. [Consultado el 20 de febrero del 2021]. Disponible en: < https://www.asocoldep.edu.co/2020/03/09/las-20-carreras-mejor-pagadas-en-colombia-y-con-mayor-demanda>
[3] HERNANDEZ, Nicolás, NOVOA, Sergio. Modelo diseño del banco de prácticas. [imagen]. Ingeniería Conceptual y diseño del banco de prácticas con PLC Siemens S7 1200 y motor trifásico con carga variables. Bogotá: 2020.
[4] BUITRAGO, Jorge, RODRÍGUEZ, Jefferson. Material didáctico para el espacio académico de automatización e instrumentación para el manejo de la banda transportadora [Trabajo de grado]. Bogotá. 2021. 90p
[5] DEL CARMEN JAIME, Melissa, HERNANDES, Cindy. Control PID de la velocidad de una banda transportadora para la clasificación de objetos [Tesis de licenciatura]. Universidad Académica de ingeniería eléctrica. 30 de mayo del 2008. Zacatecas.
[6] BATIOJA, Bladimir. Automatización de un sistema de bandas transportadoras para el abastecimiento de trozas en contrachapados de Esmeraldas S.A-Codesa. [Trabajo de titulación, previo a la obtención del título de Ingeniero en Electrónica, Automatización y Control]. 10 de febrero de 2

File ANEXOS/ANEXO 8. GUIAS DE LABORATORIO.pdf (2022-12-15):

FUNDACIÓN UNIVERSITARIA DE SAN GIL UNISANGIL FACULTAD DE CIENCIAS NATURALES E INGENIERÍA INGENIERÍA ELECTRÓNICA
Soluciones Con Excelencia

GUÍAS DE LABORATORIO BANCO PARA PRÁCTICAS DE AUTOMATIZACIÓN INDUSTRIAL, CONTROL AUTOMÁTICO DE UNA BANDA TRANSPORTADORA MEDIANTE UN VARIADOR DE FRECUENCIA CON PLC

PROGRAMA INGENIERÍA ELECTRÓNICA

FUNDACIÓN UNIVERSITARIA DE SAN GIL

UNISANGIL

SEDE YOPAL

GUIA #1

Asignatura:
Código:
Área:
Línea: | BÁSICAS DE INGENIERÍAS
Título del laboratorio: | ARRANQUE, PARADA E INVERSION DE GIRO DE UN MOTOR ELECTRICO TRIFASICO MEDIANTE UN VARIADOR DE FRECUENCIA NIETZ NL1000-02R2G2.

Docente:

OBJETIVO

- Configurar los parámetros básicos del motor a controlar según su placa de características en el VSD
- Realizar la configuración y las conexiones necesarias para el arranque de un motor eléctrico trifásico mediante un VSD.
- Realizar la configuración y las conexiones necesarias para la inversión de giro de un motor eléctrico trifásico mediante un VSD.

MARCO TEÓRICO:

Según el sitio web ALDAKIN: La automatización industrial es el uso de tecnologías para el control y monitoreo de procesos industriales, aparatos, dispositivos o máquinas, que por regla general son funciones repetitivas haciendo que funcionen automáticamente reduciendo al máximo la intervención humana. se trata de automatizar las tareas y procesos repetitivos, fatigosos, o molestos y dejar que sean las máquinas quienes los hagan.

- Variador de Frecuencia
Según el sitio web S&P: Los variadores o convertidores de frecuencia son sistemas que se encuentran entre la fuente de alimentación eléctrica y los motores eléctricos. Sirven para regular la velocidad de giro de los motores de corriente alterna (AC). Por sus siglas en inglés, solemos referirnos al variador de frecuencia como VFD, que viene de variable frequency drive, que se traduciría literalmente como “regulador/variador de frecuencia variable”. A pesar de ello, también están presentes en el mercado otras acepciones como puede ser VSD (variable speed drive o regulador de velocidad variable) o ASD (adjustable speed drive, conocido en castellano como “accionamiento de velocidad variable). Regulando la frecuencia de la electricidad que recibe el motor, el variador de frecuencia consigue ofrecer a este motor la electricidad demandada, evitando así la pérdida de energía, o lo que es lo mismo, optimizando el consumo.

Este variador estará conectado a las salidas digitales del PLC y las señales de salida de VFD estarán conectadas al motor para así controlar los Hz de velocidad de giro del eje del motor y así mismo de la velocidad de la banda.

- Controlador Lógico Programable
Un controlador lógico programable, más conocido por sus siglas en inglés PLC (Programable Logic Controller), se trata de una computadora, utilizada en la ingeniería automática o automatización industrial, para automatizar procesos electromecánicos, tales como el control de la maquinaria de la fábrica en líneas de montaje o atracciones mecánicas. Sin embargo, la definición más precisa de estos dispositivos es la dada por la NEMA (Asociación Nacional de Fabricantes Eléctricos) que dice que un PLC es: “Instrumento electrónico, que utiliza memoria programable para guardar instrucciones sobre la implementación de determinadas funciones, como operaciones lógicas, secuencias de acciones, especificaciones temporales, contadores y cálculos para el control mediante módulos de E/S analógicos o digitales sobre diferentes tipos de máquinas y de procesos”.

El controlador lógico programable será el que genere las salidas digitales para el variador de frecuencia, se desarrolla un programa en TIA PORTAL y se cargará al PLC con una Lógica para controlar la velocidad del motor.

- Motor.
Según el sitio web TRANSELEC: Un motor eléctrico es una máquina capaz de convertir la energía eléctrica en mecánica. El motor es capaz de realizar esto gracias a la acción de los campos magnéticos que generan las bobinas que se encuentran dentro del motor.


MATERIALES O EQUIPOS:
✓ Multímetro Digital
✓ BANCO PARA PRÁCTICAS DE AUTOMATIZACIÓN INDUSTRIAL, CONTROL AUTOMÁTICO DE UNA BANDA TRANSPORTADORA MEDIANTE UN VARIADOR DE FRECUENCIA CON PLC
✓ Cables cortos y largos con conexión rápida banana macho.
✓ Demás materiales necesarios
PROCEDIMIENTO
- Leer y analizar el MANUAL DE USUARIO, MANUAL TECNICO y comprender los PLANOS del banco de laboratorio.
- Leer y analizar el manual técnico del variador Nietz NL1000-02R2G2.
- Seleccionar el parámetro P101 que permite configurar la manera en que va a manipular el valor de frecuencia (velocidad), con el que trabajará el motor. Se puede configurar con 6 modos, para esta práctica se realizara seleccionando la opción, 0, 3 y 4.
0: Ajuste de frecuencia digital.
1: Voltaje analógico (0 a 10 V CD).
2: Corriente analógica (0 a 20 mA CD).
3: Perilla de ajuste (Panel de operación). La frecuencia se controla desde la perilla del panel de operación, en el rango entre las frecuencias mínima y máxima configuradas.
4: Ajuste de frecuencia ARRIBA/ABAJO.
5: Ajuste de frecuencia por comunicación RS485.
- Realizar la conexión: Panel de control – Motor para las opciones 3 y 4 del parámetro P101.
- Dar arranque, detener e invertir el giro del motor, en cada una de las configuraciones seleccionadas.

3: Perilla de ajuste (Panel de operación). La frecuencia se controla desde la perilla del panel de operación, en el rango entre las frecuencias mínima y máxima configuradas.
4: Ajuste de frecuencia ARRIBA/ABAJO.
- Realizar un programa que le permita arrancar, detener e invertir el giro del motor mediante entradas digitales (pulsadores y botón de parada de emergencia) y salidas digitales que alimentaran los contactores y a su vez controlaran el VSD para la opción 0 del parámetro P101. *Realizar las conexiones: Panel de control – Motor y demás que el estudiante considere en su programa.

Informe:
✓ Demostrar el arranque, parada e inversión de giro del motor del BANCO
PARA | PRÁCTICAS | DE | AUTOMATIZACIÓN | INDUSTRIAL, | CONTROL
AUTOMÁTICO DE UNA BANDA TRANSPORTADORA MEDIANTE UN VARIADOR DE FRECUENCIA CON PLC.

✓ Documentar su funcionalidad.

FECHAS DE ENTREGA: El estudiante debe entregar un informe detallado enformato IEEE con las conclusiones, evidencias correspondientes 8 días después de realizada la práctica.
REFERENCIAS:
https://giac.com.mx/configvariador/

GUIA #2

Asignatura:
Código:
Área:
Línea: | BÁSICAS DE INGENIERÍAS
Título del laboratorio: | DIFERENCIA DE SENSORES: SENSOR DE PROXIMIDAD CAPCITIVO, SENSOR DE PROXIMIDAD INDUCTIVO Y SENSOR DE PROXIMIDAD DE REFLEXION DIFUSA INSTALADOS EN EL BANCO PARA PRÁCTICAS DE AUTOMATIZACIÓN INDUSTRIAL, CONTROL AUTOMÁTICO DE UNA BANDA TRANSPORTADORA MEDIANTE UN VARIADOR DE FRECUENCIA CON PLC

Docente:

OBJETIVO

- Analizar el manual técnico del variador Nietz NL1000-02R2G2.
- Configurar los parámetros básicos del motor a controlar según su placa de características en el VSD
- Realizar la configuración y las conexiones necesarias para el arranque de un motor eléctrico trifásico mediante un VSD.
- Determinar las entradas y salidas digitales del proceso
- Realizar e Implementar un programa donde pueda ajustar la detección de proximidad de los sensores instalados en el BANCO PARA PRÁCTICAS DE AUTOMATIZACIÓN INDUSTRIAL, CONTROL AUTOMÁTICO DE UNA BANDA TRANSPORTADORA MEDIANTE UN VARIADOR DE FRECUENCIA CON PLC.

MARCO TEÓRICO:

Según el sitio web ALDAKIN: La automatización industrial es el uso de tecnologías para el control y monitoreo de procesos industriales, aparatos, dispositivos o máquinas, que por regla general son funciones repetitivas haciendo que funcionen automáticamente reduciendo al máximo la intervención humana. se trata de automatizar las tareas y procesos repetitivos, fatigosos, o molestos y dejar que sean las máquinas quienes los hagan.

- Variador de Frecuencia
Según el sitio web S&P: Los variadores o convertidores de frecuencia son sistemas que se encuentran entre la fuente de alimentación eléctrica y los motores eléctricos. Sirven para regular la velocidad de giro de los motores de corriente alterna (AC). Por sus siglas en inglés, solemos referirnos al variador de frecuencia como VFD, que viene de variable frequency drive, que se traduciría literalmente como “regulador/variador de frecuencia variable”. A pesar de ello, también están presentes en el mercado otras acepciones como puede ser VSD (variable speed drive o regulador de velocidad variable) o ASD (adjustable speed drive, conocido en castellano como “accionamiento de velocidad variable). Regulando la frecuencia de la electricidad que recibe el motor, el variador de frecuencia consigue ofrecer a este motor la electricidad demandada, evitando así la pérdida de energía, o lo que es lo mismo, optimizando el consumo.

Este variador estará conectado a las salidas digitales del PLC y las señales de salida de VFD estarán conectadas al motor para así controlar los Hz de velocidad de giro del eje del motor y así mismo de la velocidad de la banda.

- Controlador Lógico Programable.
Un controlador lógico programable, más conocido por sus siglas en inglés PLC (Programable Logic Controller), se trata de una computadora, utilizada en la ingeniería automática o automatización industrial, para automatizar procesos electromecánicos, tales como el control de la maquinaria de la fábrica en líneas de montaje o atracciones mecánicas. Sin embargo, la definición más precisa de estos dispositivos es la dada por la NEMA (Asociación Nacional de Fabricantes Eléctricos) que dice que un PLC es: “Instrumento electrónico, que utiliza memoria programable para guardar instrucciones sobre la implementación de determinadas funciones, como operaciones lógicas, secuencias de acciones, especificaciones temporales, contadores y cálculos para el control mediante módulos de E/S analógicos o digitales sobre diferentes tipos de máquinas y de procesos”.

El controlador lógico programable será el que genere las salidas digitales para el variador de frecuencia, se desarrolla un programa en TIA PORTAL y se cargará al PLC con una Lógica para controlar la velocidad del motor.

- Motor.
Según el sitio web TRANSELEC: Un motor eléctrico es una máquina capaz de convertir la energía eléctrica en mecánica. El motor es capaz de realizar esto gracias a la acción de los campos magnéticos que generan las bobinas que se encuentran dentro del motor.


MATERIALES O EQUIPOS:

✓ Multímetro Digital
✓ BANCO PARA PRÁCTICAS DE AUTOMATIZACIÓN INDUSTRIAL, CONTROL AUTOMÁTICO DE UNA BANDA TRANSPORTADORA MEDIANTE UN VARIADOR DE FRECUENCIA CON PLC
✓ Cables cortos y largos con conexión rápida banana macho.
✓ Demás materiales necesarios

PROCEDIMIENTO

- Leer y analizar el MANUAL DE USUARIO, MANUAL TECNICO y comprender los PLANOS del banco de laboratorio.
- Leer y analizar el manual técnico del variador Nietz NL1000-02R2G2.
- Seleccionar el parámetro P101 que permite configurar la manera en que va a manipular el valor de frecuencia (velocidad), con el que trabajará el motor. Se puede configurar con 6 modos, para esta práctica se realizara seleccionando la opción 0.
0: Ajuste de frecuencia digital.
1: Voltaje analógico (0 a 10 V CD).
2: Corriente analógica (0 a 20 mA CD).
3: Perilla de ajuste (Panel de operación). La frecuencia se controla desde la perilla del panel de operación, en el rango entre las frecuencias mínima y máxima configuradas.
4: Ajuste de frecuencia ARRIBA/ABAJO.
5: Ajuste de frecuencia por comunicación RS485.
- Realizar un programa que le permita reconocer una señal (entrada digital) de cada uno de los sensores y así por medio de una salida digital arrancar, detener, invertir el giro, aumentar o disminuir frecuencia, salidas digitales que alimentarán los contactores y a su vez controlarán el VSD
*Realizar las conexiones: Panel de control – Motor y demás que el estudiante considere en su programa.
- Ajustar la distancia de detección de cada uno de los sensores instalados en el BANCO PARA PRÁCTICAS DE AUTOMATIZACIÓN
INDUSTRIAL, | CONTROL | AUTOMÁTICO | DE | UNA | BANDA
TRANSPORTADORA MEDIANTE UN VARIADOR DE FRECUENCIA CON PLC según su conveniencia.

Informe:
✓ Demostrar el funcionamiento de cada sensor y su rango de detección de proximidad en el BANCO PARA PRÁCTICAS DE AUTOMATIZACIÓN INDUSTRIAL, CONTROL AUTOMÁTICO DE UNA BANDA TRANSPORTADORA MEDIANTE UN VARIADOR DE FRECUENCIA CON PLC
✓ Documentar su funcionalidad.

FECHAS DE ENTREGA: El estudiante debe entregar un informe
detallado en formato | IEEE | con | las | conclusiones, | evidencias
correspondientes 8 días después de realizada la práctica.
REFERENCIAS:
https://giac.com.mx/configvariador/

GUIA #3

Asignatura:
Código:
Área:
Línea: | BÁSICAS DE INGENIERÍAS
Título del laboratorio: | CLASIFICACIÓN Y CONTEO DE PIEZAS SEGÚN SU MATERIAL (METAL O NO METAL)

Docente:

OBJETIVOS

- Analizar el manual técnico del variador Nietz NL1000-02R2G2.
- Configurar los parámetros básicos del motor a controlar según su placa de características en el VSD
- Realizar la configuración y las conexiones necesarias para el arranque de un motor eléctrico trifásico mediante un VSD.
- Determinar las entradas y salidas digitales del proceso
- Realizar la configuración y las conexiones necesarias para el control de velocidad de la banda transportadora
- Realizar e Implementar un programa que contemple las señales eléctricas proveniente de los sensores que le permita clasificar un elemento de acuerdo a su material (Metal, No metal) usando los sensores del BANCO PARA PRÁCTICAS DE AUTOMATIZACIÓN
INDUSTRIAL, | CONTROL | AUTOMÁTICO | DE | UNA | BANDA
TRANSPORTADORA MEDIANTE UN VARIADOR DE FRECUENCIA CON PLC.

MARCO TEÓRICO:

Según el sitio web ALDAKIN: La automatización industrial es el uso de tecnologías para el control y monitoreo de procesos industriales, aparatos, dispositivos o máquinas, que por regla general son funciones repetitivas haciendo que funcionen automáticamente reduciendo al máximo la intervención humana. se trata de automatizar las tareas y procesos repetitivos, fatigosos, o molestos y dejar que sean las máquinas quienes los hagan.

- Variador de Frecuencia
Según el sitio web S&P: Los variadores o convertidores de frecuencia son sistemas que se encuentran entre la fuente de alimentación eléctrica y los motores eléctricos. Sirven para regular la velocidad de giro de los motores de corriente alterna (AC). Por sus siglas en inglés, solemos referirnos al variador de frecuencia como VFD, que viene de variable frequency drive, que se traduciría literalmente como “regulador/variador de frecuencia variable”. A pesar de ello, también están presentes en el mercado otras acepciones como puede ser VSD (variable speed drive o regulador de velocidad variable) o ASD (adjustable speed drive, conocido en castellano como “accionamiento de velocidad variable). Regulando la frecuencia de la electricidad que recibe el motor, el variador de frecuencia consigue ofrecer a este motor la electricidad demandada, evitando así la pérdida de energía, o lo que es lo mismo, optimizando el consumo.

Este variador estará conectado a las salidas digitales del PLC y las señales de salida de VFD estarán conectadas al motor para así controlar los Hz de velocidad de giro del eje del motor y así mismo de la velocidad de la banda.

- Controlador Lógico Programable
Un controlador lógico programable, más conocido por sus siglas en inglés PLC (Programable Logic Controller), se trata de una computadora, utilizada en la ingeniería automática o automatización industrial, para automatizar procesos electromecánicos, tales como el control de la maquinaria de la fábrica en líneas de montaje o atracciones mecánicas. Sin embargo, la definición más precisa de estos dispositivos es la dada por la NEMA (Asociación Nacional de Fabricantes Eléctricos) que dice que un PLC es: “Instrumento electrónico, que utiliza memoria programable para guardar instrucciones sobre la implementación de determinadas funciones, como operaciones lógicas, secuencias de acciones, especificaciones temporales, contadores y cálculos para el control mediante módulos de E/S analógicos o digitales sobre diferentes tipos de máquinas y de procesos”.

El controlador lógico programable será el que genere las salidas digitales para el variador de frecuencia, se desarrolla un programa en TIA PORTAL y se cargará al PLC con una Lógica para controlar la velocidad del motor.

- Motor.
Según el sitio web TRANSELEC: Un motor eléctrico es una máquina capaz de convertir la energía eléctrica en mecánica. El motor es capaz de realizar esto gracias a la acción de los campos magnéticos que generan las bobinas que se encuentran dentro del motor.


MATERIALES O EQUIPOS:
✓ Multímetro Digital
✓ Sensores capacitivos e inductivos
✓ Actuadores
✓ BANCO PARA PRÁCTICAS DE AUTOMATIZACIÓN INDUSTRIAL, CONTROL AUTOMÁTICO DE UNA BANDA TRANSPORTADORA MEDIANTE UN VARIADOR DE FRECUENCIA CON PLC
✓ Cables cortos y largos con conexión rápida banana macho.
✓ Demás materiales necesarios

PROCEDIMIENTO

- Leer y analizar el MANUAL DE USUARIO, MANUAL TECNICO y comprender los PLANOS del banco de laboratorio.
- Leer y analizar el manual técnico del variador Nietz NL1000-02R2G2.
- Seleccionar el parámetro P101 que permite configurar la manera en que va a manipular el valor de frecuencia (velocidad), con el que trabajará el motor. Se puede configurar con 6 modos, para esta práctica se realizara seleccionando la opción 0.
0: Ajuste de frecuencia digital.
1: Voltaje analógico (0 a 10 V CD).
2: Corriente analógica (0 a 20 mA CD).
3: Perilla de ajuste (Panel de operación). La frecuencia se controla desde la perilla del panel de operación, en el rango entre las frecuencias mínima y máxima configuradas.
4: Ajuste de frecuencia ARRIBA/ABAJO.
5: Ajuste de frecuencia por comunicación RS485.
- Realizar un programa que le permita reconocer una señal (entrada digital) de cada uno de los sensores y así por medio de una salida digital arrancar, detener, invertir el giro, aumentar o disminuir frecuencia, salidas digitales que alimentarán los contactores y a su vez controlarán el VSD
*Realizar las conexiones: Panel de control – Motor y demás que el estudiante considere en su programa.
- Ajustar la distancia de detección de cada uno de los sensores instalados en el BANCO PARA PRÁCTICAS DE AUTOMATIZACIÓN
INDUSTRIAL, | CONTROL | AUTOMÁTICO | DE | UNA | BANDA
TRANSPORTADORA MEDIANTE UN VARIADOR DE FRECUENCIA CON PLC según su conveniencia.

Informe:
✓ Demostrar el funcionamiento del control automático de la banda transportadora en función de la clasificación de elementos de metal y no metal desarrollado en el BANCO PARA PRÁCTICAS DE AUTOMATIZACIÓN INDUSTRIAL, CONTROL AUTOMÁTICO DE UNA BANDA TRANSPORTADORA MEDIANTE UN VARIADOR DE FRECUENCIA CON PLC
✓ Documentar su funcionalidad.

FECHAS DE ENTREGA: El estudiante debe entregar un informe
detallado en formato | IEEE | con | las | conclusiones, | evidencias
correspondientes 8 días después de realizada la práctica.
REFERENCIAS:
https://giac.com.mx/configvariador/

GUIA #4

Asignatura:
Código:
Área:
Línea: | BÁSICAS DE INGENIERÍAS
Título del laboratorio: | CONTADOR DE CANASTAS CON UN DETERMINADO NÚMERO DE BOTELLAS.

Docente:

OBJETIVO

- Analizar el manual técnico del variador Nietz NL1000-02R2G2.
- Configurar los parámetros básicos del motor a controlar según su placa de características en el VSD.
- Realizar la configuración y las conexiones necesarias para el arranque de un motor eléctrico trifásico mediante un VSD.
- Determinar las entradas y salidas digitales del proceso
- Realizar la configuración y las conexiones necesarias para el control de velocidad de la banda transportadora
- Realizar e implementar un programa que permita simular un proceso industrial de dos estaciones. En la primera estación debe realizar un conteo de botellas y cada vez que el sensor detecte una botella detendrá la banda trasportadora justo en la siguiente estacionen. La segunda estación se debe colocar la tapa de metal para seguir el curso normal del proceso. Al pasar un determinado número de botellas por las dos estaciones se llenará una canasta. Realizar el programa para contar 4 canastas de 4 botellas con tapa de metal y al finalizar este proceso se debe devolver las canastas cambiando la dirección de la banda transportadora y su frecuencia del BANCO PARA PRÁCTICAS DE AUTOMATIZACIÓN INDUSTRIAL, CONTROL AUTOMÁTICO DE UNA BANDA TRANSPORTADORA MEDIANTE UN VARIADOR DE FRECUENCIA CON PLC.

MARCO TEÓRICO:

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


MATERIALES O EQUIPOS:
✓ Multímetro Digital
✓ BANCO PARA PRÁCTICAS DE AUTOMATIZACIÓN INDUSTRIAL, CONTROL AUTOMÁTICO DE UNA BANDA TRANSPORTADORA MEDIANTE UN VARIADOR DE FRECUENCIA CON PLC
✓ Cables cortos y largos con conexión rápida banana macho.
✓ Demás materiales necesarios
PROCEDIMIENTO
- Leer y analizar el MANUAL DE USUARIO, MANUAL TECNICO y comprender los PLANOS del banco de laboratorio.
- Leer y analizar el manual técnico del variador Nietz NL1000-02R2G2.
- Seleccionar el parámetro P101 que permite configurar la manera en que va a manipular el valor de frecuencia (velocidad), con el que trabajará el motor. Se puede configurar con 6 modos, para esta práctica se realizara seleccionando la opción 0.
0: Ajuste de frecuencia digital.
1: Voltaje analógico (0 a 10 V CD).
2: Corriente analógica (0 a 20 mA CD).
3: Perilla de ajuste (Panel de operación). La frecuencia se controla desde la perilla del panel de operación, en el rango entre las frecuencias mínima y máxima configuradas.
4: Ajuste de frecuencia ARRIBA/ABAJO.
5: Ajuste de frecuencia por comunicación RS485.

*Realizar las conexiones: Panel de control – Motor y demás que el estudiante considere en su programa.

- Realizar e implementar un programa que permita simular un proceso industrial de dos estaciones. En la primera estación debe realizar un conteo de botellas y cada vez que el sensor detecte una botella detendrá la banda trasportadora justo en la siguiente estacionen. La segunda estación se debe colocar la tapa de metal para seguir el curso normal del proceso. Al pasar un determinado número de botellas por las dos estaciones se llenará una canasta. Realizar el programa para contar 4 canastas de 4 botellas con tapa de metal y al finalizar este proceso se debe devolver las canastas cambiando la dirección de la banda transportadora y su frecuencia del BANCO PARA PRÁCTICAS DE AUTOMATIZACIÓN INDUSTRIAL, CONTROL AUTOMÁTICO DE UNA BANDA TRANSPORTADORA MEDIANTE UN VARIADOR DE FRECUENCIA CON PLC.

*Realizar las conexiones: Panel de control – Motor y demás que el estudiante considere en su programa.

*Ajustar la distancia de detección de cada uno de los sensores instalados en el BANCO PARA PRÁCTICAS DE AUTOMATIZACIÓN
INDUSTRIAL, | CONTROL | AUTOMÁTICO | DE | UNA | BANDA
TRANSPORTADORA MEDIANTE UN VARIADOR DE FRECUENCIA CON PLC según su conveniencia.


Informe:
✓ Demostrar la simulación de la automatización de un proceso industrial condicionado por el conteo, tapado y llenado de canastas utilizando el BANCO PARA PRÁCTICAS DE AUTOMATIZACIÓN INDUSTRIAL, CONTROL AUTOMÁTICO DE UNA BANDA TRANSPORTADORA MEDIANTE UN VARIADOR DE FRECUENCIA CON PLC.
✓ Documentar su funcionalidad.

FECHAS DE ENTREGA: El estudiante debe entregar un informe
detallado en formato | IEEE | con | las | conclusiones, | evidencias
correspondientes 8 días después de realizada la práctica.
REFERENCIAS:

https://www.youtube.com/watch?v=i0q6o5H8MpI

https://drive.google.com/file/d/1Vv3oh4VyXtCipiyf5hOqXKAayLl0SHc/view?usp=sharing

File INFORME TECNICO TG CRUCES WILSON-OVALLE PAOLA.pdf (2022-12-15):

BANCO PARA PRÁCTICAS DE AUTOMATIZACIÓN INDUSTRIAL, CONTROL AUTOMÁTICO DE UNA BANDA TRANSPORTADORA MEDIANTE UN VARIADOR DE FRECUENCIA CON PLC

WILSON SNEIDER CRUCES CORREA PAOLA ANDREA OVALLE FORERO

FUNDACIÓN UNIVERSITARIA DE SAN GIL - UNISANGIL FACULTAD DE CIENCIAS NATURALES E INGENIERÍA INGENIERÍA ELECTRÓNICA
YOPAL- CASANARE
2022

BANCO PARA PRÁCTICAS DE AUTOMATIZACIÓN INDUSTRIAL, CONTROL AUTOMÁTICO DE UNA BANDA TRANSPORTADORA MEDIANTE UN VARIADOR DE FRECUENCIA CON PLC

WILSON SNEIDER CRUCES CORREA PAOLA ANDREA OVALLE FORERO

Proyecto de grado presentado para optar el título de: INGENIERO ELECTRÓNICO.

Director
Tobías Cárdenas Rodríguez
Especialista en Instrumentación y control Industrial

FUNDACIÓN UNIVERSITARIA DE SAN GIL “UNISANGIL” FACULTAD DE CIENCIAS NATURALES E INGENIERÍA INGENIERÍA ELECTRÓNICA
YOPAL – CASANARE
2022

NOTA DE ACEPTACIÓN

________________________________ ________________________________ ________________________________ ________________________________ ________________________________ ________________________________ ________________________________

________________________________ Firma del presidente del jurado.

________________________________ Firma del jurado.

________________________________ Firma del jurado.

Yopal, 02 de Noviembre 2022

Dedicamos este proyecto a todas las personas que fueron inspiración y apoyo durante el recorrido de este largo camino de nuestra formación profesional.

Principalmente, a nuestras familias, que fueron la fuente de motivación para iniciar este proceso de formación y pilar de la fortaleza necesaria para culminarla.

A nuestros padres, que nos aportaron las bases necesarias tanto en aprendizaje como en formación personal para enfrentar cada uno de los retos puestos durante las diferentes fases de desarrollo de la ingeniería.

Por último, a la fundación universitaria Unisangil y toda su comunidad, empezando desde cada uno de nuestros compañeros hasta todos aquellos docentes que con paciencia y dedicación compartieron sus conocimientos y destrezas que nos ayudaron a enriquecer no solo en nuestra formación como ingenieros electrónicos, si no también, nuestra formación integral como seres humanos.

Agradecimientos, al ingeniero Tobías Cárdenas Rodríguez, director de proyecto de grado, quien a través de su destreza como especialista en Instrumentación y control Industrial compartió su conocimiento y nos apoyó técnicamente durante el desarrollo del mismo.

Al ingeniero Wilson Gómez, director del programa de Ingeniería Electrónica Unisangil sede Yopal, por su apoyo incondicional durante el transcurso y desarrollo de nuestra formación profesional.

Al ingeniero Daniel Albarracín, por su asistencia técnica en la elaboración documental de este proyecto, como también por su acompañamiento profesional durante nuestra formación como ingenieros electrónicos.

Finalmente, a la Fundación Universitaria Unisangil y a toda su comunidad por brindarnos la oportunidad de formarnos profesionalmente.

Contenido

4. DESARROLLO | LA | PLATAFORMA | TRABAJO | DE | LA | BANDA
5. DISEÑO E IMPLEMENTACIÓN DE LA ESTRUCTURA DEL BANCO DE
6. DESARROLLO EL PROGRAMA PARA EL CONTROLADOR LÓGICO

6.1 | DISEÑO | 37
6.2 | IMPLEMENTACIÓN | 37
7. DISEÑO DE GUÍAS DE LABORATORIO APLICATIVAS AL BANCO DE
PRACTICAS | 43
8. PRUEBAS DE FUNCIONAMIENTO | 61
9. CONCLUSIONES | 64
10. BIBLIOGRAFÍA | 66
11. RECOMENDACIONES | 68
12. ANEXOS | 69

LISTA DE FIGURAS
Pág.
Figura 1. Módulo didáctico para el control de presión, temperatura y nivel | 16

Figura 2. Diseño de un banco de prácticas de PLC y variador de velocidad con motor

eléctrico trifásico | 17

Figura 3. Material didáctico para el espacio académico de automatización e

instrumentación para el manejo de la banda transportadora | 17
Figura 4. prototipo de una banda transportadora | 18
Figura 5. Automatización de un sistema de bandas transportadoras | 19
Figura 6. Diseño final de la banda transportadora | 21
Figura 7. Diseño final de los componentes | 22
Figura 8. Diseño final de plataforma de trabajo de la banda transportadora | 22
Figura 9. Piezas modulares | 23
Figura 10. Ejes de desplazamiento | 24
Figura 11. Piezas modulares de la banda transportadora | 25
Figura 12. plataforma de trabajo en madera | 25

Figura 13. Presentación de la banda transportadora en estructura de madera. ....26

Figura 26. Estructura segundo segmento desplazamiento de la banda lado derecho.

Figura 31. Segmento control de detención de la banda por parada de emergencia.

LISTA DE ANEXOS

ANEXO 1. FICHA TÉCNICA Siemens HMI, KTP700 BASIC, BASIC PANEL 6AV2 123-2GB03-0AX0.

ANEXO 2. FICHA TÉCNICA PLC Siemens S7-1200

ANEXO 3. FICHA TÉCNICA FUENTE SDN 10-24-100C

ANEXO 4. FICHA TÉCNICA SWITCH Siemens SCALANCE XB005 -6GK50050BA001AB2

ANEXO 5: FICHA TÉCNICA VFD NL1000- user manual Eng 2016-01

ANEXO 6: DISEÑOS

ANEXO 7: CÓDIGO DEL PROGRAMA

ANEXO 8 GUÍAS DE LABORATORIO

ANEXO 9. VIDEO TUTORIAL PRUEBA DE FUNCIONALIDAD GUÍA DE LABORATORIO

### 1. RESUMEN

El siguiente documento contiene el desarrollo del diseño e implementación de un banco para prácticas de automatización aplicando control automático a una banda transportadora mediante un variador de frecuencia controlado por PLC , este proyecto además de su estructura física, cuenta con guías de laboratorio, manual de usuario y planos eléctricos que le permitirá a los estudiantes de la Fundación Universitaria Unisangil sede Yopal, interactuar y poner en práctica los conocimientos teóricos adquiridos en las diferentes áreas de la ingeniería tales como
instrumentación | industrial, | maquinas | rotativas, | programación, | control | y
automatización de procesos, mediante el desarrollo de prácticas de laboratorio.

Este proyecto está compuesto por una estructura de trabajo que contiene una banda transportadora, un variador de frecuencia, un reductor de giro 10:1, un motor 0.4 Hp y finalmente integrado aun módulo de PLC/HMI disponible en el laboratorio de electrónica.

La finalidad de este proyecto, en presente, la realizado es construir un banco de prácticas de automatización que será suministrado al laboratorio de prácticas de la Fundación Universitaria Unisangil sede Yopal y a todos los ingenieros en formación, con el objetivo de contribuir a la formación integra teórico práctica, fortaleciendo los conocimientos y así mismo las competencias de profesionales del egresado en ingeniería electrónica de la Unisangil.

Palabras claves: automatización Industrial, PLC, variador de frecuencia, motor, variador de giro.

### 1.1 ABSTRACT

The following document contains the development of the design and implementation of a bench for automation practices applying automatic control to a conveyor belt through a PLC-controlled frequency inverter, laboratory, this project, in addition to its physical structure, has laboratory guides, a user manual and electrical plans that will allow the students of the Yopal Unisangil University Foundation to interact and put into practice the theoretical knowledge acquired in the different areas of engineering such as industrial instrumentation, rotating machines, programming, control and process automation, through the development of laboratory practices.

This project is composed of a work structure that contains a conveyor belt, a frequency variator, a 10:1 rotation reducer, a 0.4 Hp motor and finally an integrated PLC/HMI module available in the electronics laboratory.

The purpose of this project, in present, the one carried out is to build a bank of automation practices that will be supplied to the laboratory of practices of the Unisangil University Foundation headquarters Yopal and to all the engineers in training, with the aim of contributing to the integral theoretical and practical training, strengthening the knowledge and likewise the competences of professionals of the graduate in electronic engineering of the Unisangil.

Keywords: industrial Automation, Plc, frequency inverter, motor, rotation variator.

### 2. INTRODUCCIÓN

GSL industrias¹ define la automatización industrial como el uso de sistemas computarizados, electromecánicos, electro neumáticos y electrohidráulicos para fines industriales. Dentro de las ramas de ingeniería, es uno de los procesos más completos y transversales a diferentes actividades industriales a nivel nacional.

El presente trabajo de grado, da a conocer el proceso de diseño e implementación de banco para prácticas de automatización aplicando control automático a una banda transportadora mediante un variador de frecuencia controlado a través de un PLC, con el objetivo de que en un futuro permita a estudiantes de carreras universitarias afines, desarrollar sus prácticas en las áreas de instrumentación industrial, maquinas rotativas, programación, control y automatización de procesos.

Una vez se implemente el proyecto, quedará disponible para que los profesionales en formación puedan valerse de él para afianzar sus conocimientos ya que podrá ser aplicado en el desarrollo de laboratorios no solo de la ingeniería electrónica sino también de programas de formación afines, además, servirá de base para futuras mejoras o innovaciones,

1 GSL INDUSTRIAS. Que es la automatización industrial [Artículo en línea]. 18 de noviembre de 2020. Disponible en: < https://industriasgsl.com/blogs/automatizacion/que-es-la-automatizacion-industrial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,y%20electrohidr%C3%A1ulicos%20para%20fines%20industriales (https://industriasgsl.com/blogs/automatizacion/que-es-la-automatizacion-industrial) >

### 3. REQUERIMIENTOS

3.1 . PLANTEAMIENTO DEL PROBLEMA

### 3.1.1. Situación problemática. En Colombia según datos de Asocoldep²

la
ingeniería Electrónica está dentro de las carreras mejor pagadas y con mayor demanda en vinculación laboral con un promedio del 84.4%. Convirtiéndola en una buena opción de formación profesional. La accesibilidad a estas carreras universitarias es relativamente fácil, además hay un número considerable de universidades que ofrecen diferentes programas profesionales de ingenierías, estando al alcance de cualquier joven con aspiraciones de aprendizaje en estas áreas. Dentro de estas entidades de formación existe una problemática, que interfiere en el proceso de formación de estos profesionales y se trata de la falta de espacios adecuados y laboratorios que les permita a los ingenieros electrónicos en formación desarrollar sus conocimientos, aplicarlos y relacionarlos en los campos de la instrumentación industrial, electrónica de potencia, diseño electrónico, control y automatización.

La Fundación Universitaria de San Gil UNISANGIL sede Yopal, cuenta con un amplio grupo de jóvenes interesados en los diferentes programas de formación, una de ellas la ingeniería electrónica. Esta ingeniería es una carrera profesional con bastante exigencia, su etapa de teoría como la práctica, son muy importantes a la hora de pensar en ser un excelente profesional. Teniendo en cuenta lo anterior la sede UNISANGIL Yopal viene trabajando en fortalecer sus espacios de laboratorio de tal manera que les brinde a sus estudiantes un ambiente de aprendizaje apropiado dotado con recursos que permita realizar las prácticas de laboratorio, espacio esencial para el proceso de formación profesional

### 3.1.2. Formulación del problema ¿La construcción de un banco para prácticas de

automatización industrial, control automático de una banda transportadora mediante un variador de frecuencia con PLC, ayudará a los estudiantes de ingeniería electrónica a mejorar sus habilidades en el desarrollo de prácticas de programación de PLC y automatización?

2 ASOCOLDEP. ¿Cuáles son las carreras universitarias más demandadas y mejor pagadas en Colombia? [En línea]. 2020. [Consultado el 20 de febrero del 2021]. Disponible en: < https://www.asocoldep.edu.co/2020/03/09/las-20-carreras-mejor-pagadas-en-colombia-y-con-mayor-demanda>

### 3.2 JUSTIFICACIÓN

Una de las principales áreas de desempeño de un ingeniero electrónico es la automatización y control de procesos; los procesos automatizados en la actualidad tienen una alta demanda ya que el diseño de estos sistemas van enfocados al mejoramiento y optimización del mismo, teniendo en cuenta lo anterior, se considera de vital importancia que la Fundación Universitaria de San Gil Unisangil cuente con espacios de laboratorios adecuados que les permita a los ingenieros en formación interactuar con equipos, sistemas y tecnologías implementadas en las áreas de Instrumentación, control y automatización, tales como el controlador lógico programable.

Pensando en la calidad de formación del ingeniero electrónico, la Fundación Universitaria Unisangil sede Yopal ha venido mejorando los espacios laboratorio de electrónica, hasta el momento varios estudiantes que están finalizando su proceso de formación, como trabajo de grado, han desarrollado e implementado diferentes bancos de prácticas; con el fin de seguir contribuyendo con la adecuación y equipamiento de esta área tan importante el en proceso de formación de los ingenieros electrónicos, nace la idea de diseñar un banco para prácticas de automatización industrial, en este caso, el control automático de una banda transportadora mediante un variador de frecuencia con PLC. Este nuevo banco para practicas quedará al servicio del laboratorio de la universidad y para uso de todos los estudiantes del programa de ingeniería electrónica, de esta manera la Fundación Universitaria de San Gil UNISANGIL mejorará tanto su laboratorio como la calidad de formación que ofrece a sus profesionales.

### 3.3 OBJETIVOS

### 3.3.1 Objetivo general. Diseñar e implementar un banco para prácticas de

automatización aplicando control automático a una banda transportadora mediante un variador de frecuencia con PLC.

### 3.3.2 Objetivos específicos

- Desarrollar la plataforma de trabajo de la banda transportadora.

- Diseñar y realizar la estructura del banco de prácticas, donde se integre la banda transportadora y el motor junto con su control automático
- Desarrollar el programa para el controlador lógico programable que permita la automatización del proceso mediante el variador de frecuencia.
- Realizar pruebas de funcionalidad del sistema para verificar su correcto funcionamiento y de esta manera alcanzar el objetivo principal del proyecto.
- Diseñar cuatro guías de laboratorio que les permita a los estudiantes interactuar con el banco de prácticas y conocer cada uno de los sistemas que lo componen.

### 3.4 ESTADO DEL ARTE

En la fundación universitaria Unisangil sede Yopal, los Ingenieros en formación le han apostado a contribuir con el equipamiento de los espacios de laboratorio de la ingeniería, con el desarrollo e implementación de bancos para prácticas de neumática, electro neumático, modulo variador de frecuencia, banco de procesos industriales, entre otros, estos proyectos, además de permitirle a los ingenieros en formación aplicar sus conocimientos con ejecución de estos, también contribuyen a la formación de todos los estudiantes de ingeniería electrónica de la facultad, creando espacios apropiados para fomentar sus conocimientos mediante el desarrollo practico de guías de laboratorio aplicativas a los bancos implementados en el laboratorio; en el años 2016 fue desarrollado por dos estudiantes de ingeniería electrónica como proyecto de grado el diseño e implementación de un módulo didáctico para el control de presión, temperatura y nivel dirigido hacia las áreas de instrumentación industrial, control y automatización del programa de ingeniería electrónica de UNISANGIL, en la siguiente figura se puede observar el banco de procesos industriales implementado.

Figura 1. Módulo didáctico para el control de presión, temperatura y nivel.


Fuente. FUNDACIÓN UNIVERSITARIA DE SAN GIL-UNISANGIL.

En la Universidad Antonio Nariño de Bogotá, dos estudiantes de Ingeniería Electromecánica desarrollaron como proyecto de grado un banco didáctico, se trata del diseño de un banco de prácticas donde se integra un controlador lógico programable, un VFD con motor eléctrico trifásico y fue implementado en el laboratorio de automatización de la facultad. EL principio de funcionamiento de este banco de prácticas se basa en que la carga variable del motor está condicionada por el cambio de temperatura de un fluido en función de su viscosidad, de tal manera el sistema realiza la supervisión de la temperatura del fluido por medio del PLC. Durante el proceso de diseño los estudiantes realizaron el análisis de diferentes variables eléctricas presentes en la operación del banco con el fin de identificar los parámetros a ajustar en el variador de velocidad para controlar las RPM del motor. Con la implementación de este proyecto se buscó incentivar el desarrollo de prácticas orientadas al uso de equipos de programación industrial con el objetivo principal de afianzar conceptos y adquirir nuevas destrezas; teniendo en cuenta la aplicación de este banco de prácticas, está diseñado para operar con un motor trifásico con potencia máxima 0,37 kW a una tensión de 220 V ac, el sistema de control y monitoreo integrado por PLC, variador, sensores y pulsadores se encuentran instalados en una estructura con dimensiones 1,20 metros de ancho, 60 cm de alto y con profundidad de 30 cm además, se realizan los manuales de ensamblaje en sitio de todos los componentes del banco de prácticas e instructivo de puesta en servicio, también los correspondientes archivos de programación para la parametrización del controlador lógico programable y el variador de velocidad³

3 HERNANDEZ, Nicolás, NOVOA, Sergio. Modelo diseño del banco de prácticas. [imagen]. Ingeniería Conceptual y diseño del banco de prácticas con PLC Siemens S7 1200 y motor trifásico con carga variables. Bogotá: 2020.

Figura 2. Diseño de un banco de prácticas de PLC y variador de velocidad con motor eléctrico trifásico.


Fuente. HERNANDEZ, Nicolás, NOVOA, Sergio. Modelo diseño del banco de prácticas. [imagen]. Ingeniería Conceptual y diseño del banco de prácticas con PLC Siemens S7 1200 y motor trifásico con carga variables. Bogotá: 2020.

Por su parte, como lo refiere Buitrago & Rodríguez⁴
, en la universidad Santo Tomas estos dos estudiantes de la facultad de ingeniería mecánica desarrollaron como proyecto de grado un material didáctico para el espacio académico de la facultad aplicado al área de automatización e instrumentación, es este caso se trata de la elaboración de dos guías de prácticas donde se diseña la automatización de dos procesos industriales diferentes, los estudiantes realizan la simulación del proceso automático de empaquetamiento de productos , el control automático de calidad y el desarrollo de la programación del controlador lógico programable para la automatización de los dos procesos anteriormente nombrados.

Figura 3. Material didáctico para el espacio académico de automatización e instrumentación para el manejo de la banda transportadora.

4 BUITRAGO, Jorge, RODRÍGUEZ, Jefferson. Material didáctico para el espacio académico de automatización e instrumentación para el manejo de la banda transportadora [Trabajo de grado]. Bogotá. 2021. 90p.

Fuente. BUITRAGO, Jorge, RODRÍGUEZ, Jefferson. Material didáctico para el espacio académico de automatización e instrumentación para el manejo de la banda transportadora [Trabajo de grado]. Bogotá. 2021. 90p..

De la misma, en la Universidad Autónoma de Zacatecas Francisco García Salinas, dos estudiantes presentaron como tesis de licenciatura un control de velocidad de una banda transportadora para la clasificación de objetos. Este proyecto se llevó a cabo a partir de la construcción de un prototipo de una banda transportadora, impulsada por un motor de corriente directa a 24 V, el control de velocidad de la banda transportadora está condicionada con la implementación de diferentes sensores y un código de programación para el controlador lógico programable PLC S7-200 de SIEMENS⁵

Figura 4. prototipo de una banda transportadora.

Fuente. DEL CARMEN JAIME, Melissa, HERNANDES, Cindy. Control PID de la velocidad de una banda transportadora para la clasificación de objetos [Tesis de licenciatura]. Universidad Académica de ingeniería eléctrica. 30 de mayo del 2008. Zacatecas.

Finalmente, como lo realizó Batioja⁶ en su trabajo de titulación, sobre la Automatización de un sistema de bandas transportadoras para el abastecimiento de trozas en Contrachapados de Esmeraldas S.A – Codesa, el proyecto consistió en realizar la automatización del sistema de bandas transportadoras mediante el uso de un PLC Siemens 1200, sensores mecánicos, fotoeléctricos, dispositivos de maniobra, operación, protección y actuadores rotativos y lineales. Para realizar

5 DEL CARMEN JAIME, Melissa, HERNANDES, Cindy. Control PID de la velocidad de una banda transportadora para la clasificación de objetos [Tesis de licenciatura]. Universidad Académica de ingeniería eléctrica. 30 de mayo del 2008. Zacatecas.
6 BATIOJA, Bladimir. Automatización de un sistema de bandas transportadoras para el abastecimiento de trozas en contrachapados de Esmeraldas S.A-Codesa. [Trabajo de titulación, previo a la obtención del título de Ingeniero en Electrónica, Automatización y Control]. 10 de febrero de 2022.

operaciones de supervisión, alertas tempranas de fallas y control de unas cuantas variables se incluirá un interfaz humano máquina HMI. La fábrica Contrachapado de Esmeraldas S.A – Codesa opera principalmente con un suministro de energía de 220/380 VAC, por lo cual los equipos, dispositivos y actuadores deben considerar esta especificación eléctrica.

Figura 5. Automatización de un sistema de bandas transportadoras


Fuente. BATIOJA, Bladimir. Automatización de un sistema de bandas transportadoras para el abastecimiento de trozas en contrachapados de Esmeraldas S.A-Codesa. [Trabajo de titulación, previo a la obtención del título de Ingeniero en Electrónica, Automatización y Control]. 10 de febrero de 2022.

En base al estado del arte consultado, se evidencia que la implementación de un banco didáctico para prácticas en los espacios de laboratorio, resultan muy útiles, ya que les permite a los estudiantes interactuar con los diferentes sistemas reforzando sus conocimientos y competencias como ingenieros; el desarrollo e implementación de este tipo de proyectos tienen un grado de aceptación bien significativa por parte Universidades que ofrecen este tipo de programas teniendo en cuenta su interés por brindar una educación con buenos estándares de calidad.

### 3.5 DESCRIPCIÓN DE LA SOLUCIÓN

El desarrollo de este proyecto se localizará en el laboratorio de ingeniería electrónica de la Fundación Universitaria de San Gil UNISANGIL sede Yopal Casanare, corresponde al Desarrollo Tecnológico Curricular; con la implementación de este banco de prácticas se beneficiará los 156 ingenieros en formación al periodo 2021-1

7 y todos los nuevos estudiantes de pregrado de Ingeniería Electrónica, de la facultad de ciencias Naturales e ingeniería, ya que contando con este banco para prácticas en el laboratorio de Electrónica les permitirá a los estudiantes complementar sus conocimientos mediante el desarrollo de prácticas de laboratorio con guías aplicativas a las asignaturas de: máquinas rotativas, control digital e instrumentación industrial, fortaleciendo así las competencias de cada uno de los ingenieros en formación.

La automatización de procesos cada día es más importante en la industria, por tal motivo, un ingeniero con buenas conocimiento y competencias en esta área, contara con un amplio ámbito para ejecución de su profesión, las entidades universitarias que ofrecen la formación en estas ingenierías siempre le apuestan brindar a sus estudiantes una buena formación profesional, teniendo en cuenta lo anterior, se evidencia que el desarrollo e implementación de bancos de prácticas didácticos en una buena alternativa.

Conocer un PLC, sus partes, funciones, programarlo y comprobar su funcionamiento es un proceso fundamental para enriquecer los conocimientos de un ingeniero electrónico en formación. “La industrialización y las necesidades de producción han creado la necesidad de automatizar más y más procesos para hacerlos más eficientes”

8
. Y dentro de las competencias de un ingeniero electrónico esta la automatización de procesos industriales con diferentes tipos de controladores, en especial PLC's como los más apetecidos por la industria. Este banco de prácticas contará con un amplio campo aplicativo para desarrollo de diferentes prácticas de laboratorio.

7 VORTAL. Dirección de Programa. [En línea]. 2021. [Consultado el 22 de febrero del 2021]. Disponible en: < https://vortal.unisangil.edu.co/unisangil/hermesoft/vortal/login.jsp>.
8 FREELANCERMAP. ¿Qué hace un ingeniero en automatización? [En línea]. 2020. [Consultado el 26 de febrero del 2021]. Disponible en: <https://www.freelancermap.com/blog/es/que-hace-ingeniero-automatizacion/>

### 4. DESARROLLO LA PLATAFORMA TRABAJO DE LA BANDA

TRANSPORTADORA

4.1 DISEÑO.

Inicialmente, se realiza el diseño de la plataforma de trabajo de la banda transportadora a mano alzada, teniendo en cuenta que las dimensiones sean proporcional las medidas del banco de prácticas y el espacio del laboratorio donde será instalado finalmente, sus dimensiones son de 1 metro de largo, 17,5 centímetros de ancho y 10 cm de alto , Con ayuda de la herramienta informática Thinkercad se monta el diseño verificando una presentación adecuada estéticamente y funcional, en la siguiente figura se puede observar el diseño de la plataforma de trabajo con sus dimensiones.

Figura 6. Diseño final de la banda transportadora.


Fuente: Elaboración propia.

Así mismo, se realiza el diseño de cada uno de los componentes de la banda transportadora, entre ellos el mecanismo de empuje, el rodillo accionado o impulsado, rodamientos, el engranaje y la estructura de física del sistema, su diseño también fue realizado con ayuda de la herramienta Thinkercad, en la siguiente figura se muestra el diseño de los componentes de la banda transportadora.

Figura 7. Diseño final de los componentes.


Fuente: Elaboración propia.

Finalmente, ya con el diseño de la banda transportadora y cada una de sus partes, se realiza un montaje en la herramienta Thinkercad donde se integra cada uno de los componentes, se realiza la presentación y se valida que el diseño de la plataforma está de acuerdo al fin deseado, en la siguiente figura se muestra el diseño final de la plataforma de trabajo de la banda transportadora.

Figura 8. Diseño final de plataforma de trabajo de la banda transportadora.


Fuente: Elaboración propia.

### 4.2 IMPLEMENTACIÓN

Buscando minimizar los costos del proyecto y garantizando la calidad de los componentes, se planeó realizar la mayoría de las partes de la plataforma de trabajo, en impresión 3D con filamento PLA, se imprimieron 8 engranajes los cuales son los elementos encargados de permitir el giro o mecanismo de desplazamiento de la banda, estos engranajes irán montados con la distribución de 2 por cada eje; el diseño de la banda o faja tiene una dimensión de 2,10 metros de larga por 17.5 centímetros de ancha, para construir la banda con esas dimensiones fue necesario la impresión en 3D de 154 piezas modulares, estas piezas modulares fueron diseñadas con unas pestañas las cuales encajan con los dientes del engranaje, el objetivo de este sistema es movilizar la banda en paralelo al giro del engranaje; para el soporte de los ejes se diseñaron 4 soportes intermedio y 4 soportes para los extremos, estos elementos serán los encargados de fijar y asegurar cada uno de los 4 ejes del sistema de desplazamiento de la banda, en la siguiente figura se muestra las partes de la plataforma de trabajo impresas en dimensión 3D.

Figura 9. Piezas modulares.

Fuente: Elaboración propia.

Dentro del diseño del mecanismo de giro o desplazamiento de la banda se contempla el uso de 4 ejes en material de acero plata, este material se considera adecuado ya que es resistente y de buena apariencia física, cada eje es de 19 cm aproximadamente, uno de estos ejes recibe el nombre de mecanismo de empuje el cual será accionado por reductor de giro 10:1 conectado al motor de 0.4 Hp. En cada eje ira instalado 2 engranajes; en el diseño del mecanismo de desplazamiento de la plataforma de trabajo para la banda transportadora se ve necesario incluir un sistema de rodamientos, se emplean un total de 12 rodamientos 608 2RS distribuidos de la siguiente manera, 4 rodamientos soldados a la estructura metálica los cuales influyen en la alienación de la banda, 8 instalados en los ejes del sistema de desplazamiento, en la siguiente figura se muestra el tipo de eje y rodamiento usado.

Figura 10. Ejes de desplazamiento.


Fuente: Elaboración propia.

Las 154 piezas modulares junto con cada uno de los componentes requeridos para la plataforma de trabajo entre ellos, 8 engranajes, 3 rodillos, 4 soportes intermedio del eje, 4 soporte de extremo del eje, 6 ejes de soporte para los rodillos, se construyen de manera satisfactoria según el diseño a base de filamento PLA impreso en dimensión 3D, las piezas modulares se integraron con radios de bicicleta ya que es un material resistente y apropiado para la finalidad de su uso.

Figura 11. Piezas modulares de la banda transportadora.

Fuente: Elaboración propia.

Con el fin de validar la resistencia de cada uno de los componentes impresos en PLA, el correcto funcionamiento y realizar una presentación provisional, se construye una estructura para la plataforma de trabajo de la banda transportadora en material amaderado, su construcción se realiza teniendo en cuenta el diseño inicial y las dimensiones contempladas, tal como se muestra en la siguiente figura.

Figura 12. plataforma de trabajo en madera


Fuente: Elaboración propia.

Se integra cada uno de los componentes armando la plataforma de trabajo sobre la estructura de madera, se valida resistencia del material, correcto funcionamiento y presentación adecuado de acuerdo al diseño inicial, lo anterior se realizó acondicionado un motor trifásico de 0.4 Hp al rodillo de empuje de la banda; durante el desarrollo de esta prueba de funcionamiento se evidencia la necesidad de implementar un reductor de velocidad con el fin de aumentar la frecuencia de operación del motor ya que la frecuencia actual oscila entre 0 a 20 Hz, adicionalmente, se observa que en la parte inferior de la banda se forma un seno accionando fricción con la estructura, por tal motivo es necesario implementar unos rodillos adicionales para mantener la firmeza de la banda y así eliminar la fricción observada, se diseñan 3 rodillos y se construyen a base de filamento PLA impreso en dimensión 3D, adicionalmente para garantizar el mecanismo de giro de los rodillos se implementan 6 rodamientos 608 2RS más, en la siguiente figura se observa la presentación de la plataforma de trabajo acoplado al mecanismo de giro de la banda.

Figura 13. Presentación de la banda transportadora en estructura de madera.


Fuente: Elaboración propia.

Como proceso final para alcanzar el primer objetivo planteado y luego de validar el funcionamiento correcto de la plataforma de trabajo para la banda transportadora, se procede a realizar el montaje de la estructura final en material metálico, integrando cada uno de los componentes fabricados en filamento PLA impreso en 3D anteriormente relacionados, los 18 rodamientos 608 2RS y los 4 ejes de 19 cm aprox, como se muestra en la siguiente figura.

Figura 14. Montaje final plataforma de trabajo de la banda transportadora.


Fuente: Elaboración propia.

### 5. DISEÑO E IMPLEMENTACIÓN DE LA ESTRUCTURA DEL BANCO DE

PRÁCTICAS.

### 5.1 DISEÑO

Teniendo en cuenta la importancia de contar con un escenario cómodo, adaptable al espacio del laboratorio de electrónica de la facultad y basado en los tamaños de los bancos de prácticas existentes, se diseña una estructura para el banco de prácticas con dimensiones de 1,20 metros de largo y un ancho de 71,5 centímetros, basado en otro aspecto y no menos importante como son los espacios de trabajo adecuados ergonómicamente, este banco de prácticas se diseña con una altura de 85 centímetros, apostando a la comodidad del usuario; La estructura del banco de prácticas de automatización está diseñada de tal manera que permite la instalación de manera estética y adecuación de cada uno de los equipos que lo componen tales como el motor, reductor de giro y la plataforma de trabajo de la banda transportadora.

Figura 15. Diseño de la estructura de banda transportadora.


Fuente: Elaboración propia

Adicionalmente el diseño de la estructura del banco cuenta con un espacio libre el cual puede ser usado por los estudiantes como escritorio o en su defecto, para integrar a bancos de prácticas disponibles en la facultad o acondicionar a nuevas ideas para el desarrollo de proyectos, el diseño de este espacio tiene las dimensiones mostradas en la siguiente Figura.

Figura 16. Dimensiones de las tablas de la mesa de trabajo.


Fuente: Elaboración propia

El banco para prácticas de automatización industrial, también cuenta con el diseño de una estructura donde se instala el sistema de control del proceso, las dimensiones de esta estructura se definen teniendo en cuenta el espacio requerido para la instalación de cada uno del componente del sistema de control tales como el controlador lógico programable, el VFD, switch, pantalla HMI, la fuente regulador, accesorios y la distribución de entradas y salidas, el tamaño diseñado también es proporcional a las dimensiones del banco de prácticas teniendo en cuenta el espacio para su instalación; en la siguiente figura se muestra el diseño de la estructura con dimensiones.

Figura 17. Estructura del sistema de control.

Fuente: Elaboración propia

Para las líneas de alimentación del banco de prácticas, se diseña un plano eléctrico con la distribución de la alimentación adecuada para cada equipo, se implementó un interruptor tripolar el cual alimenta en variador, las 3 fases de alimentación del motor esta derivada desde el variador, el panel de control esta alimentado de una de las fases del motor por medio de un interruptor de 10 A, este interruptor es el general del panel de control, el cual también alimenta la fuente.

Figura 18. Plano de distribución eléctrica AC.


Fuente: Elaboración propia

La fuente de voltaje tiene 2 salidas de 24 v, una de ellas conectada a un interruptor de 6 A, la cual controla 24 v y la línea a tierra del lado derecho del panel de control, la otra salida esta conecta a un interruptor de 3 A, de punto de conexión se deriva la alimentación para los 5 fusibles implementados para PLC, switch,HMI, entradas digitales y salidas digitales.

Figura 19. Plano de distribución eléctrica DC.


Fuente: Elaboración propia

### 5.2 EQUIPOS

Dentro de los equipos que componen el banco para prácticas de automatización industrial, control automático de una banda transportadora mediante un variador de frecuencia con PLC tenemos:

Motor eléctrico. esta máquina rotativa es la encargada de convertir la energía eléctrica en energía mecánica, para el desarrollo de este proyecto se implementa un motor trifásico asíncrono o de inducción de 0.4 Hp, marca SIEMENS, con serie 1LA3, frecuencia de 60 Hz, velocidad nominal de 1640 rpm, la selección del motor se realiza teniendo en cuenta el peso de la banda transportadora diseñada ya que este es el mecanismo de giro el banco de prácticas

Figura 19. Motor eléctrico, mecanismo de giro.


Fuente: Elaboración propia

Reductor de velocidad: en la prueba de funcionalidad de la plataforma de trabajo se identificó la necesidad de implementar un reductor de giro con el fin de mejorar la frecuencia de operación del motor, sin el reductor de velocidad la banda operaria a una velocidad muy alta aproximada a la velocidad nominal del motor a 60 Hz, se realiza la adaptación de un reductor de velocidad 10:1, para conectar el motor con el reductor se requirió 1 acople el cual fue fabricado en material nylon.

Figura 20. Reductor de velocidad.


Fuente: Elaboración propia
Para control automático de una banda transportadora mediante un variador de frecuencia con PLC, se utilizó VFD NL1000 este variador de frecuencia se escogió teniendo en cuenta su bajo costo comparado con otros en el mercado, además, aunque en este banco de prácticas se usan solo las entradas digitales este VFD tiene otras formas de operación las cuales podrán ser usadas en futuras innovaciones del proyecto, otro aspecto tenido en cuenta es el tamaño, fácil instalación y cableado.

Figura 21. Variador de frecuencia.


Fuente: Elaboración propia

El sistema de control de la banda transportadora además del VFD está compuesto por un módulo de control disponible en el laboratorio de electrónica de la Universidad, este módulo consta de una pantalla HMI SIMATIC HMI, KTP700 Basic, un Switch Siemens SCALANCE XB005, un PLC Siemens S7-1200 y una fuente de alimentación SDN 10-24-100C, cada uno de estos equipos son instalados en la estructura diseñada para el panel de control del banco.

### 5.3 IMPLEMENTACIÓN

Teniendo en cuenta el diseño y medidas de la estructura del banco para prácticas, con ayuda de un ornamentador se realiza el corte de cada una de las partes de la estructura, se unen con material soldado apropiada para el material, las terminación y uniones son pulidas cuidadosamente para evitar bordes filosos o con potencial de daño para los usuarios, finalmente con el objetivo una mejor presentación estética de la estructura y conservación del material metálico se le aplico base anticorrosiva y una capa de laca color aluminio. En la siguiente figura se muestra el resultado final la estructura del banco de prácticas construido.

Figura 22. Estructura final banco de prácticas.

Fuente: Elaboración propia

La estructura para el sistema de control se construye a partir del diseño inicial, esta estructura es elaborada en material aluminio, algunas partes en materia acero inoxidable y acrílico, en esta estructura se acondiciona el PLC/HMI, el variador de frecuencia VFD, la fuente reguladora, el switch y cada uno de los accesorios requeridos para la adecuación de las señales de entradas y salidas del módulo de control, adicionalmente, cuenta con un espacio para la identificación del banco, allí se realiza la instalación de una placa que fue diseñada e impresa con el número y nombre del banco como se puede evidenciar en la siguiente figura.

Figura 23. Estructura para el sistema de control.


Fuente: Elaboración propia

Como resultado final se obtiene la estructura del banco de prácticas con medidas acordes y buena presentación física, se integra cada uno de los componentes del banco entre ellos la plataforma de trabajo de la banda transportadora, el motor con reductor de giro y el módulo de control, se realiza la instalación y adecuación de los cables de conexión para las diferentes señales del sistema, cada uno de los dispositivos fueron conectados, finalmente se cumple con el segundo objetivo general del proyecto.

Figura 24. Estructura para el sistema de control.


Fuente: Elaboración propia.

### 6. DESARROLLO EL PROGRAMA PARA EL CONTROLADOR LÓGICO

PROGRAMABLE

### 6.1 DISEÑO

El programa planteado a continuación simula el control de una banda transportadora mediante un variador de frecuencia (VFD) siendo accionado por pulsadores para el inicio, parada, cambio de giro y una parada de emergencia, todo comandado desde un controlador lógico programable (PLC). Que toma como entrada las señales de los pulsadores y entrega una señal de control para la operación del VFD.
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

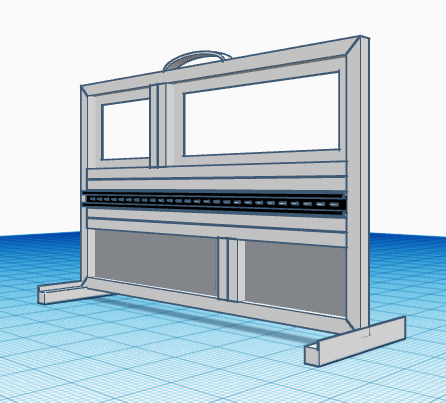
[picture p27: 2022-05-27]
DISEÑOS DE CONSTRUCCIÓN/Diseño Estructura Panel de Control/Estructura/Lateral Delantero.png

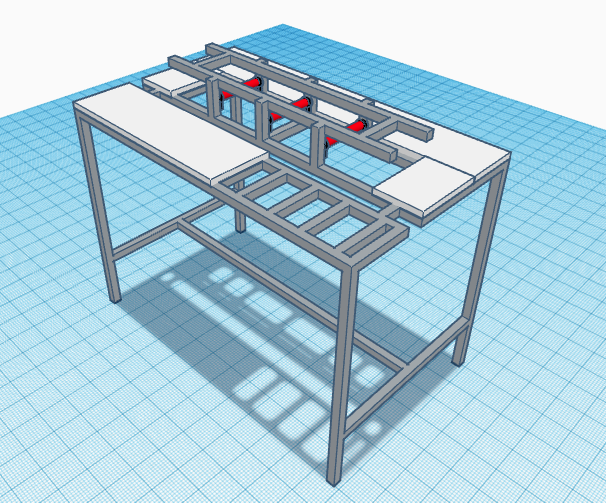
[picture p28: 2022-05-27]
DISEÑOS DE CONSTRUCCIÓN/Diseño Estructura Mesa de trabajo Banda Transportadora/Estructura, mesa y rodillos.png

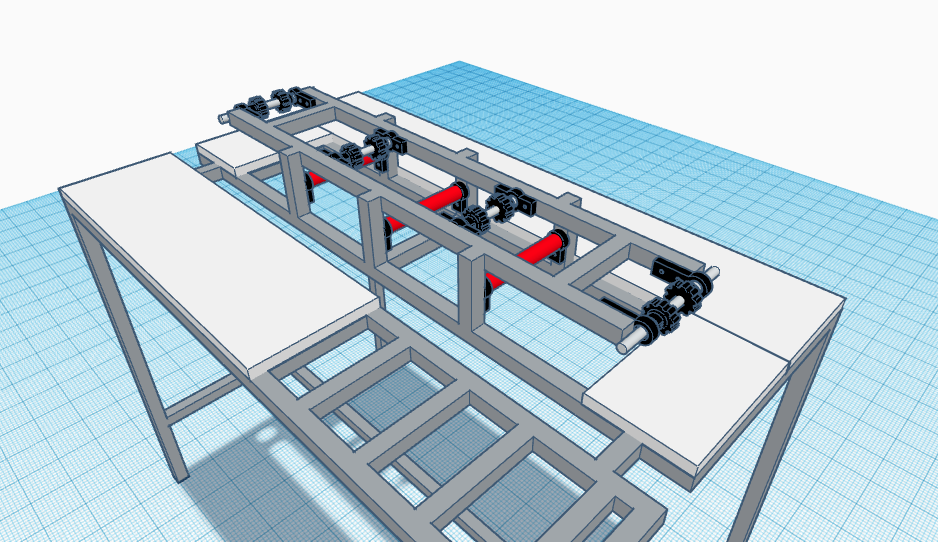
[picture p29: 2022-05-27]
DISEÑOS DE CONSTRUCCIÓN/Diseño Estructura Mesa de trabajo Banda Transportadora/Estructura, mesa, rodillos y engranajes.png

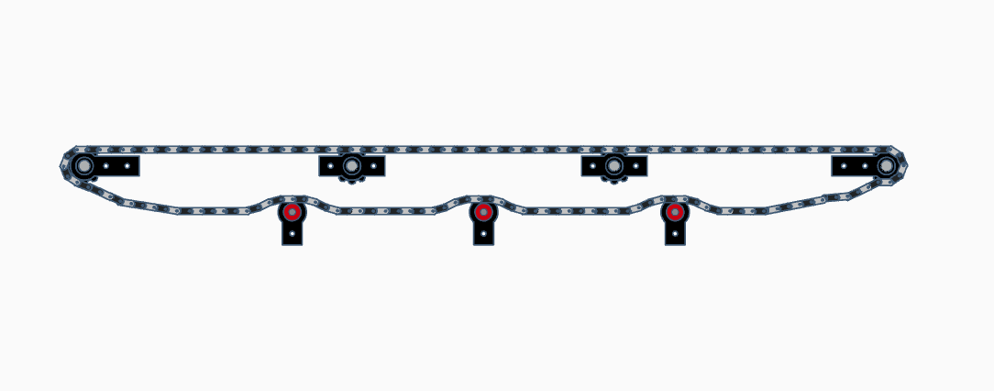
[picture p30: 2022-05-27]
DISEÑOS DE CONSTRUCCIÓN/Diseño Estructura Mesa de trabajo Banda Transportadora/Banda y mecanismo - 2.png

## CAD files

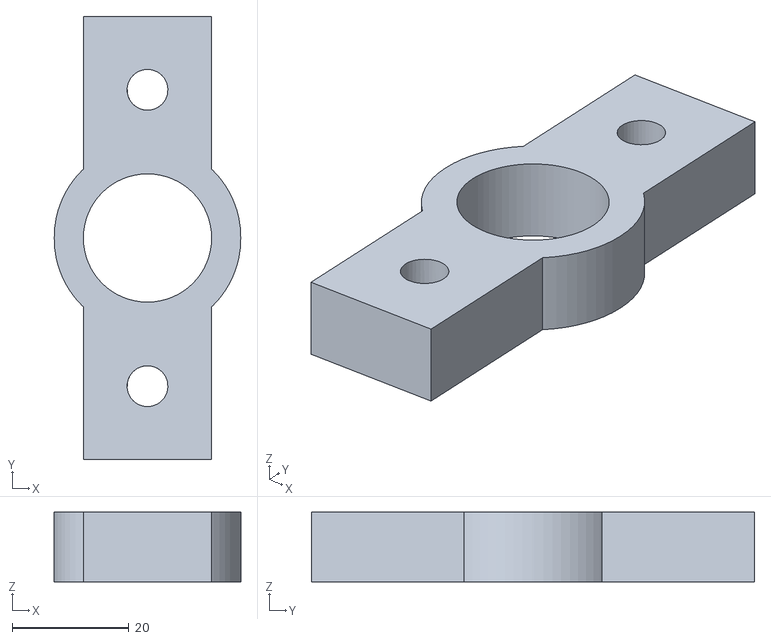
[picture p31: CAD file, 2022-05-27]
ANEXOS/ANEXO 6. DISEÑOS/Soporte Interno.stl
32.0 x 76.0 x 12.0

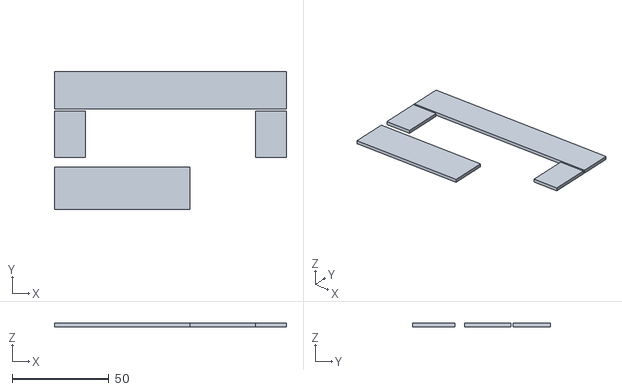
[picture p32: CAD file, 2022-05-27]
ANEXOS/ANEXO 6. DISEÑOS/Tablas.stl
120.0 x 71.5 x 1.90

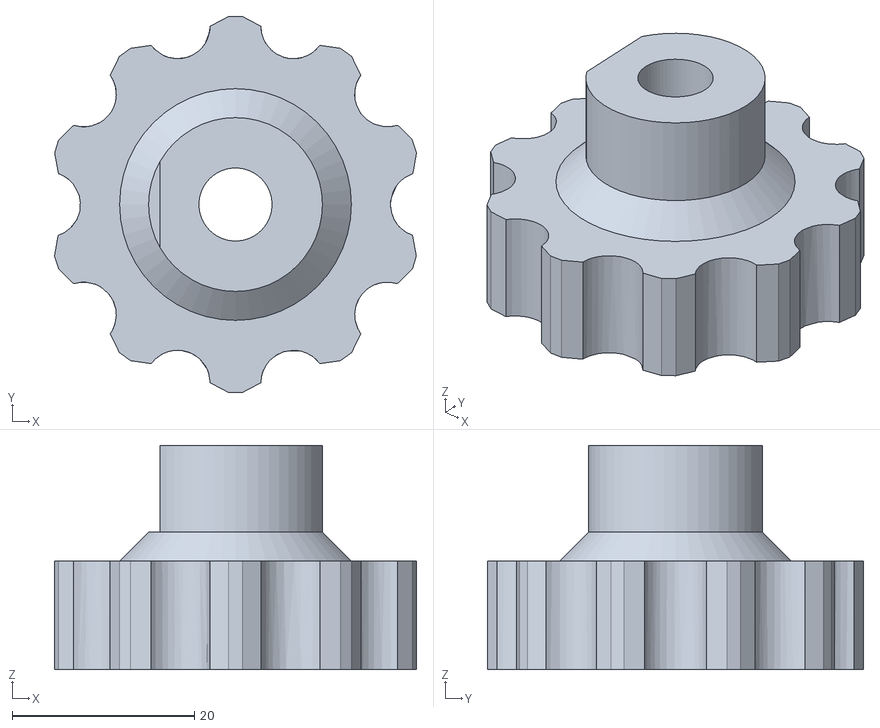
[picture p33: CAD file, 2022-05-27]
ANEXOS/ANEXO 6. DISEÑOS/Engranaje.stl
39.7 x 41.2 x 24.6

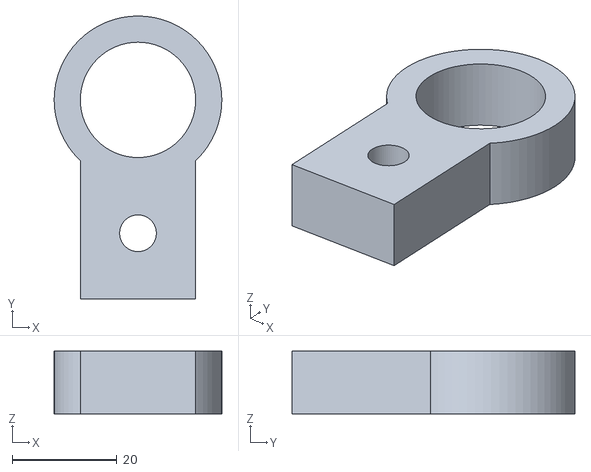
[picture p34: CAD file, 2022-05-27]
ANEXOS/ANEXO 6. DISEÑOS/Soporte Rodillo.stl
32.0 x 54.0 x 12.0

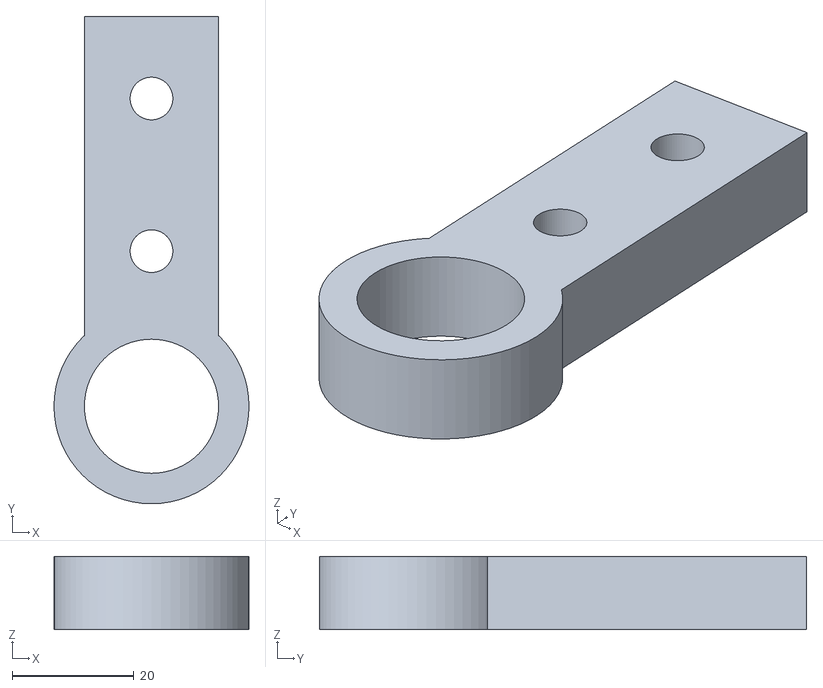
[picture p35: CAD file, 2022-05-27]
ANEXOS/ANEXO 6. DISEÑOS/Soporte Esquinas.stl
32.0 x 80.0 x 12.0

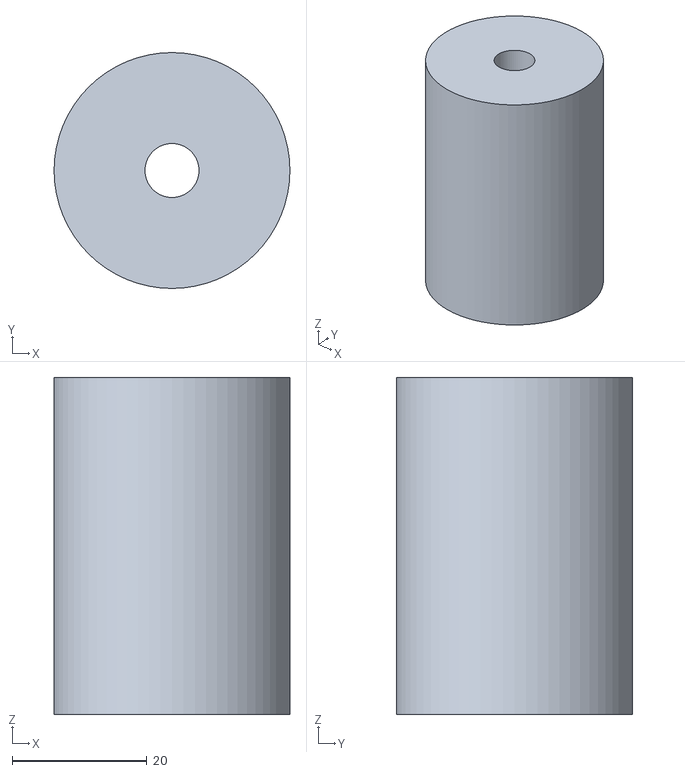
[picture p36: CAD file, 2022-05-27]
ANEXOS/ANEXO 6. DISEÑOS/Acople Motoreductor.stl
35.0 x 35.0 x 50.0

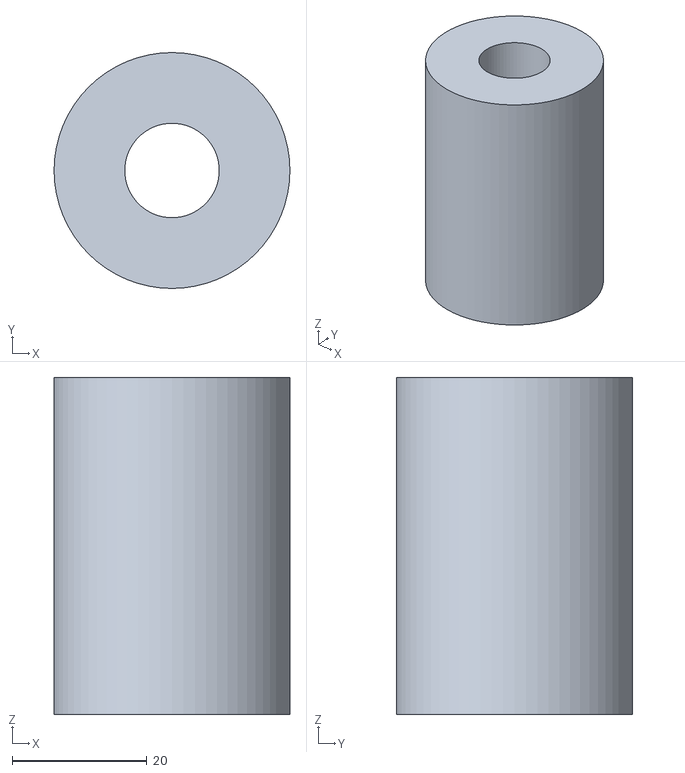
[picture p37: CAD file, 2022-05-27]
ANEXOS/ANEXO 6. DISEÑOS/Acople Reductor.stl
35.0 x 35.0 x 50.0

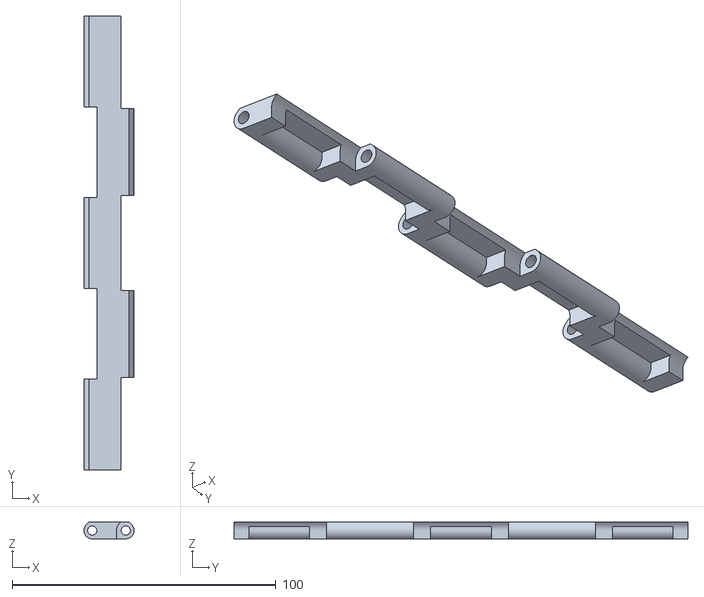
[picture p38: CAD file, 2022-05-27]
ANEXOS/ANEXO 6. DISEÑOS/Pieza - Banda.stl
19.1 x 172.0 x 6.35

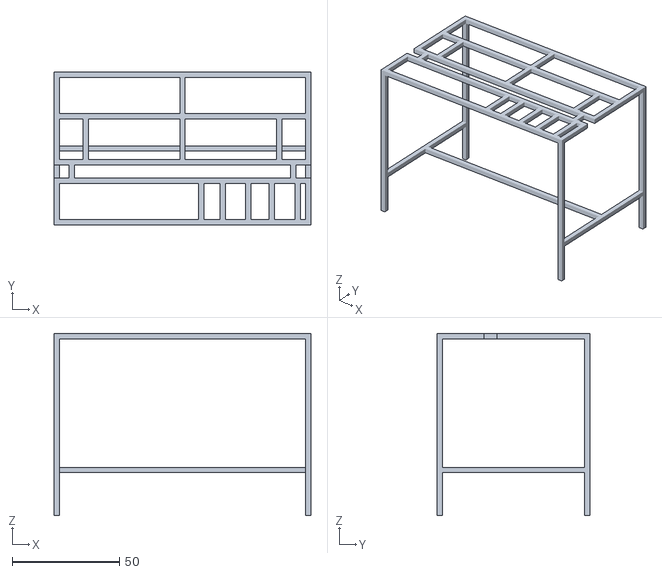
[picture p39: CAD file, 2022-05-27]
ANEXOS/ANEXO 6. DISEÑOS/Estructura de Mesa.stl
120.0 x 71.5 x 85.0

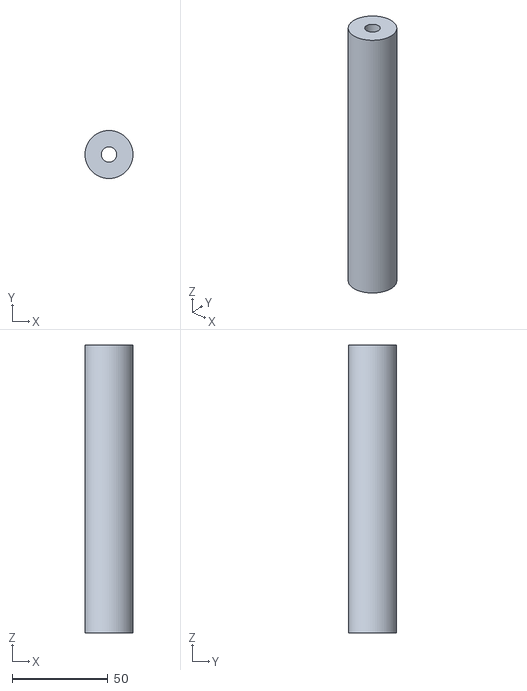
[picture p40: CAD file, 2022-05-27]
ANEXOS/ANEXO 6. DISEÑOS/Rodillo.stl
25.0 x 25.0 x 150.0

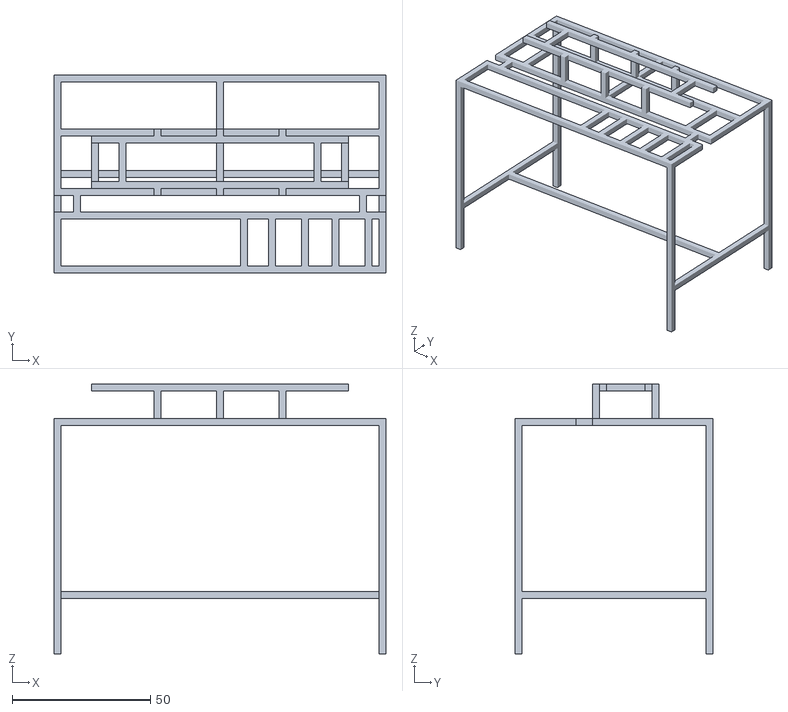
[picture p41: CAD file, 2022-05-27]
ANEXOS/ANEXO 6. DISEÑOS/Estructura Completa.stl
120.0 x 71.5 x 97.5

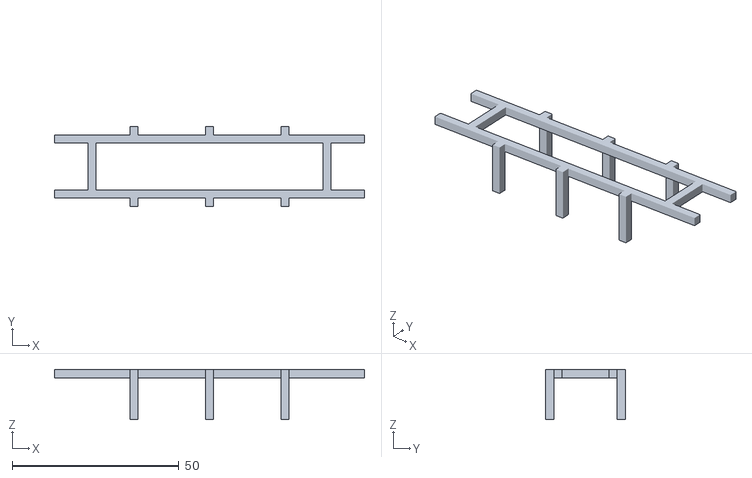
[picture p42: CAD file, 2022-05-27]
ANEXOS/ANEXO 6. DISEÑOS/Estructura de Banda.stl
93.0 x 24.0 x 15.0

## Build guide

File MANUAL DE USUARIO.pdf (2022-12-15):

BANCO | PARA | PRÁCTICAS | DE
AUTOMATIZACIÓN | INDUSTRIAL,

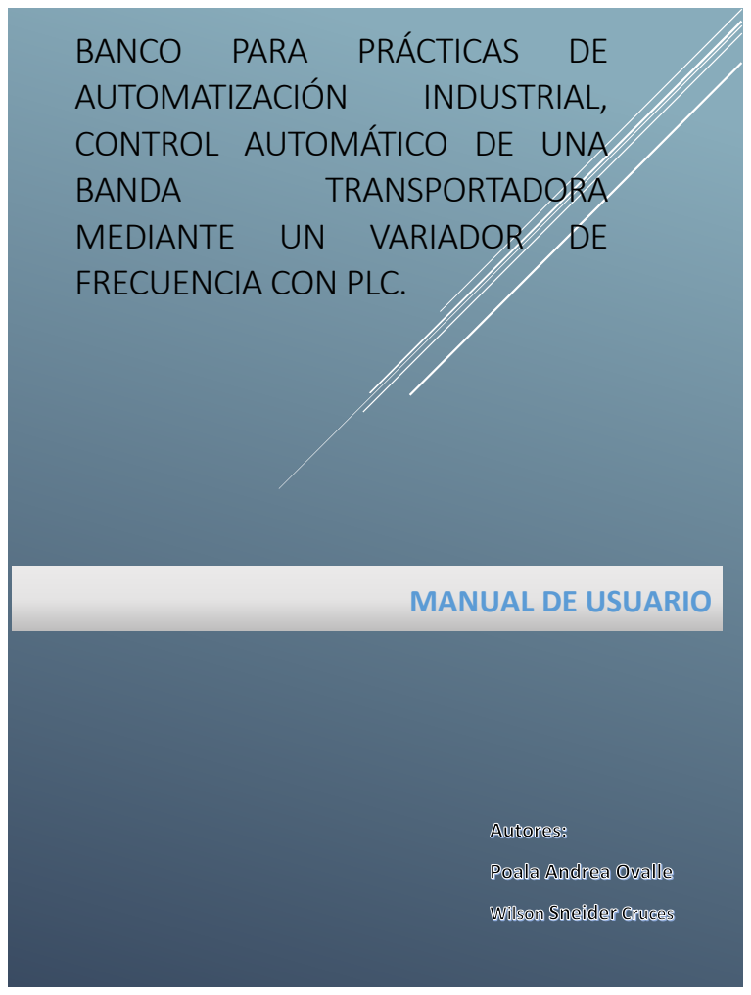
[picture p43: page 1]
BANDA; TRANSPORTADORA

CONTROL AUTOMÁTICO DE UNA
MEDIANTE UN VARIADOR DE
FRECUENCIA CON PLC.

MANUAL DE USUARIO

PELIGROS Y PREVENCIONES

Antes de manipular el banco de prácticas, conozca los riesgos a los que estas expuesto y las medidas de prevención que puedes aplicar.

✓ Riesgo eléctrico:

i. VSD: Tenga en cuenta que
VSD | se | alimenta | con
corriente alterna a 220 VAC, antes de arrancar el sistema verifique que las conexiones estén realizadas de manera
correcta; | al | finalizar | la
practica normalice el sistema dejándolo en su condición
inicial.
ii. | FUENTE | DC: | Tener
precaución, la fuente se
alimenta | con | corriente
alterna a 110 VAC, Realizar
todas | las | conexiones
pertinentes | antes | de
energizar el sistema, de igual modo en el proceso inverso.

✓ Riesgo mecánico.

i. Motor: No manipular ni
introducir objetos mientras esté en funcionamiento el
motor-reductor
ii. Banda transportadora. No se debe limpiar ni realizar
mantenimiento
manualmente sobre la banda transportadora mientras esté en movimiento y no se haya desconectado de todo tipo
de fuente de energía.

RECOMENDACIONES
PRELIMINARES

✓ Realizar lubricación con aceite 3 en 1 a los rodamientos de la banda transportadora de manera periódica (cada 15 días).

✓ | Antes | de | poner | a | operar
automáticamente | la | banda
transportadora | verificar
manualmente que al girar no esté bloqueada. Si lo está por favor desensámblela y verifique si hay alguna obstrucción o fractura en alguno de sus componentes si es así informar al auxiliar de laboratorio para su reparación.

✓ El peso máximo que puede desplazar la banda trasportadora es de 2 Kg (Según las pruebas realizadas); Por favor no exceder este peso ni intentar detener o frenarla mientras esté en funcionamiento, ya que puede averiar los engranajes o las piezas que la componen.

PROCEDIMIENTO DE USO

Luego de conocer los peligros y aplicar las medidas de prevención, continúe su práctica siguiendo el siguiente paso a paso.
1. Conecte el sistema a la fuente

de alimentación (Conexión trifásica 220 v).
2. Verifique el encendido de

VSD.

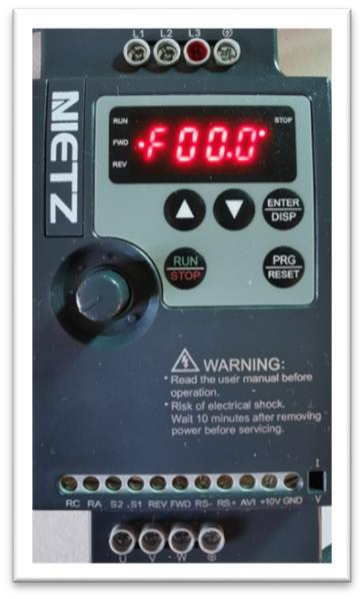
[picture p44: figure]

3. | Active | el | Breaker | para

alimentar el sistema de control.
4. Continúe con la configuración

básica del variador de frecuencia.

CONFIGURACIÓN DE PARÁMETROS DEL VARIADOR DE FRECUENCIA.

La configuración se realiza en 3 etapas: parámetros básicos del motor, método de mando, tiempos de arranque/ paro y límites de frecuencia.

- | Configuración | parámetros
| del motor:

Tecla para cambiar las decenas de los parámetros a configurar, Mantener pulsado para seleccionar.

Tecla de navegación arriba.

Tecla de navegación abajo.

Tecla para ingreso a parámetros

Teclado funcional.

Tenga en cuenta las características del motor descrita en la placa.

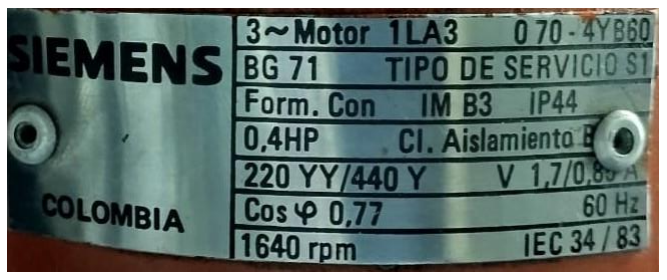
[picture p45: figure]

Pulse la tecla PROG/RESET, aparecerá en la pantalla de VSD el primer parámetro a configurar.

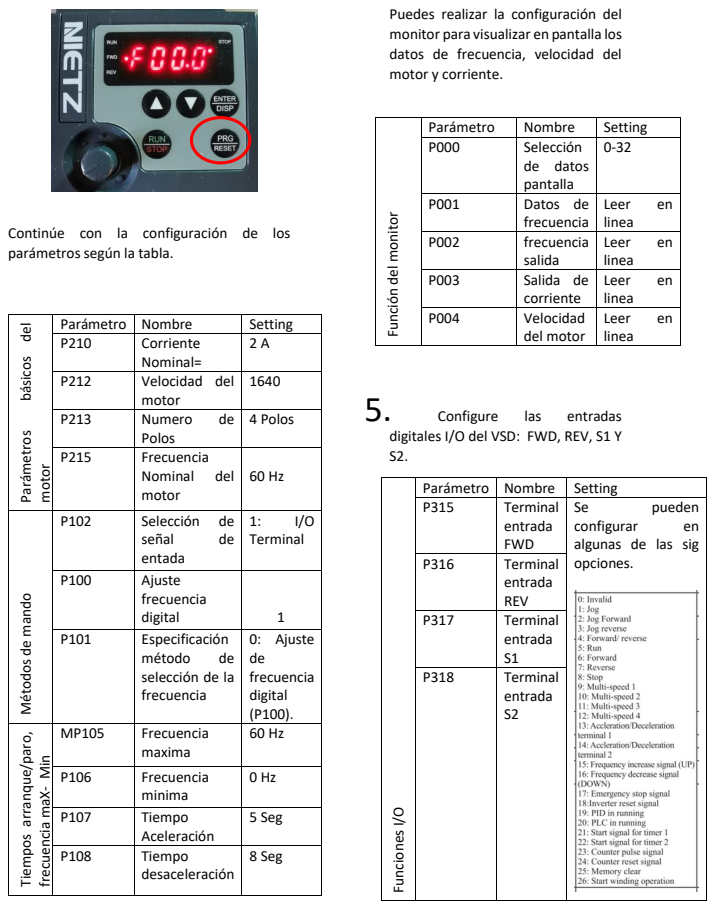
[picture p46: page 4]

Puedes realizar la configuración del
monitor para visualizar en pantalla los
datos de frecuencia, velocidad del
motor y corriente.

Parámetro | Nombre | Setting
P000 | Selección de datos pantalla | 0-32

P001 | Datos de frecuencia | Leer en linea

Continúe con la configuración de los
parámetros según la tabla.

P002 | frecuencia salida | Leer en linea

P003 | Salida de corriente | Leer en linea

P004 | Velocidad del motor | Leer en linea

P210 | Corriente Nominal= | 2 A

P212 | Velocidad del motor | 1640

P213 | Numero de Polos | 4 Polos

digitales I/O del VSD: FWD, REV, S1 Y
S2.Funciones I/O

P215 | Frecuencia Nominal del motor | 60 Hz

P315 | Terminal entrada FWD

algunas de las sig

P102 | Selección de señal de entada | 1: I/O Terminal

P100 | Ajuste frecuencia digital | 1

entrada REV

P317 | Terminal entrada S1

P101 | Especificación método de selección de la frecuencia | 0: Ajuste de frecuencia digital (P100).

P318 | Terminal entrada S2

MP105 | Frecuencia maxima | 60 Hz

P106 | Frecuencia minima | 0 Hz

P107 | Tiempo Aceleración | 5 Seg

P108 | Tiempo desaceleración | 8 Seg

Configure la frecuencia de acuerdo a la
entrada digital que se active en el VSD. Parametros de frecuencia | Parámetro | Nombre | Setting
| P503 | Multi-speed1 | 0.1-20.0
| P504 | Multi-speed2 | 0.1-10.0
| P505 | Multi-speed3 | 0.1-20.0
| P506 | Multi-speed4 | 0.1-25.0

Los valores setting puedes ajustarse de
acuerdo | al | requerimiento | de | la
implementacion.
6. Ejecute el programa del PLC Y

valide el funcionamiento del control
automático | de | la | banda
transportadora.

DIAGNOSTICO DE FALLAS

✓ | a. | Simular una entrada digital
mediante la acción del interruptor tipo codillo estando conectado un sensor afecta la lectura y puede averiarlo. Este problema sucede
debido | a | que | el | interruptor
conectacon 24 VDC para simular un pulso activo, al estar el sensor conectado a este mismo punto, dicho voltaje puede incidir en la salida del sensor afectando la lectura e incluso dañándolo. Por tal motivo, se realizó una conexión de un Diodo en serie al terminar de salida del sensor para garantizar el sentido de la señal del sensor a PLC y no del PLC a sensor.

✓ Seleccionar el tipo de contacto (NA/NC) equivocado de los sensores y pulsadores en la programación. Este es un error que puede alterar la lógica de programación, ya que puede que el sensor envíe un pulso de 0 V y no de 24 VDC cuando hay una detección; Esto no quiere decir que el sensor este mal, si no que la lógica es inversa. Por lo tanto, para el desarrollo de la programación tener en cuenta que los sensores y pulsadores del banco son del tipo:

✓

**NA: 0 VDC

**NC: 24 VDC

✓ | Seleccionar el tipo de control del VSD equivocado. El VSD cuenta con varias formas de controlar la velocidad del motor, en este caso se utiliza la forma de entrada digital accionada por contactores que son activados con las salidas digitales del PLC. Remitirse al manual para entender la lógica del funcionamiento y seleccionar este tipo de control si el VSD no responde mediante las entradas digitales.
ELEMENTO | TIPO
SENSOR DE PROXIMIDAD CAPACITIVO | NC
SENSOR DE PROXIMIDAD INDUCTIVO | NA
SENSOR DE PROXIMIDAD DE REFLEXIÓN DIFUSA | NC
PULSADOR DE COLOR VERDE (START) | NA
PULSADOR DE COLOR ROJO (STOP) | NC
BOTÓN PARADA DE EMERGENCIA | NC

NOTA: Estos son los errores más comunes que se evidenciaron en las pruebas de funcionalidad al implementar la guía N°4.

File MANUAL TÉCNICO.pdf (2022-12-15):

# MANUAL TÉCNICO

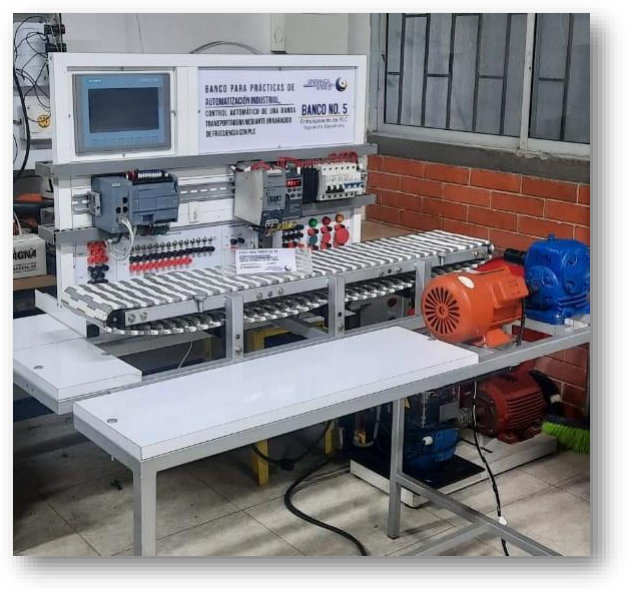
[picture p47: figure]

BANCO PARA PRÁCTICAS DE AUTOMATIZACIÓN INDUSTRIAL,

### CONTROL AUTOMÁTICO DE UNA BANDA TRANSPORTADORA

MEDIANTE UN VARIADOR DE FRECUENCIA CON PLC.

Autores:
Wilson Sneider Cruces
Paola Andrea Ovalle

CONTENIDO.

INTRODUCCIÓN

## INTRODUCCIÓN

El siguiente documento contiene la información básica detallada sobre componentes, operación, funcionamiento y cuidado mantenedor del sistema, con el fin de que el usuario final conozca de manera detallada el banco para prácticas de automatización industrial control automático de una banda transportadora con PLC.

Adicionalmente contiene los planos detallados de señales de control y potencia del sistema, para garantizar que se tenga la ingeniería inicial de construcción, como también los segmentos del programa de control para el PLC.

## OBJETIVO

- Proporcionar una guía para el usuario, del banco para prácticas de automatización aplicando control automático a una banda transportadora mediante un variador de frecuencia.

## COMPONENTES

El banco para prácticas de automatización se compone de una banda transportadora con su estructura de trabajo, construido con un material resistente acorde a su finalidad de uso, allí el usuario puede realizar diferentes prácticas de laboratorio, también cuenta con un espacio libre para modificación o uso como escritorio; la banda tiene un acople de conexión al motor.

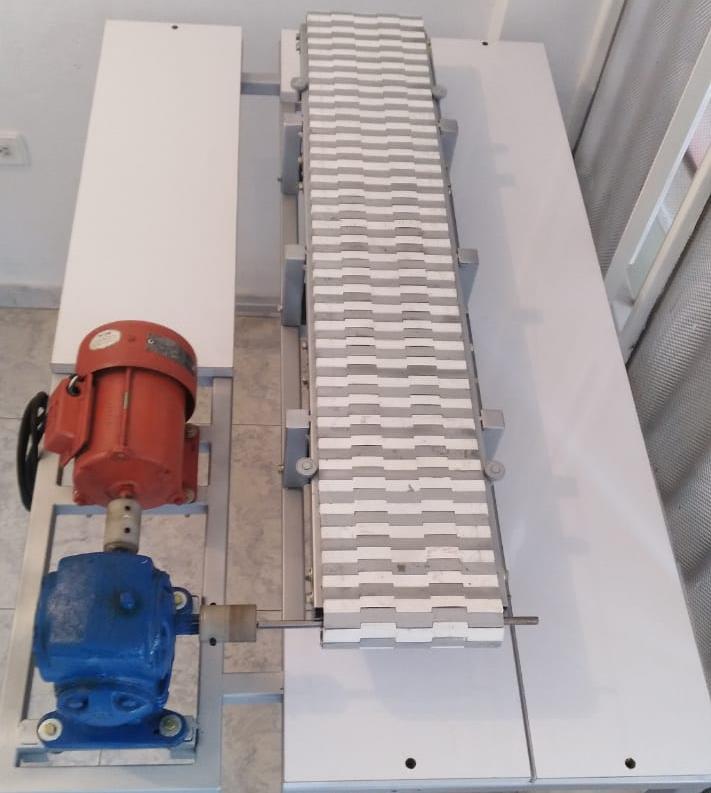
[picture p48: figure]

Fig 1: Estructura banda transportadora.

El mecanismo físico de giro del banco de prácticas lo compone un motor y reductor de giro, adicionalmente cuenta con la estructura física del sistema de control automático integrado por una fuente de voltaje 24 vdc, un variador de frecuencia, una pantalla HMI, un PLC, un Switch, contactores y adecuaciones de entradas y salidas del panel de control.

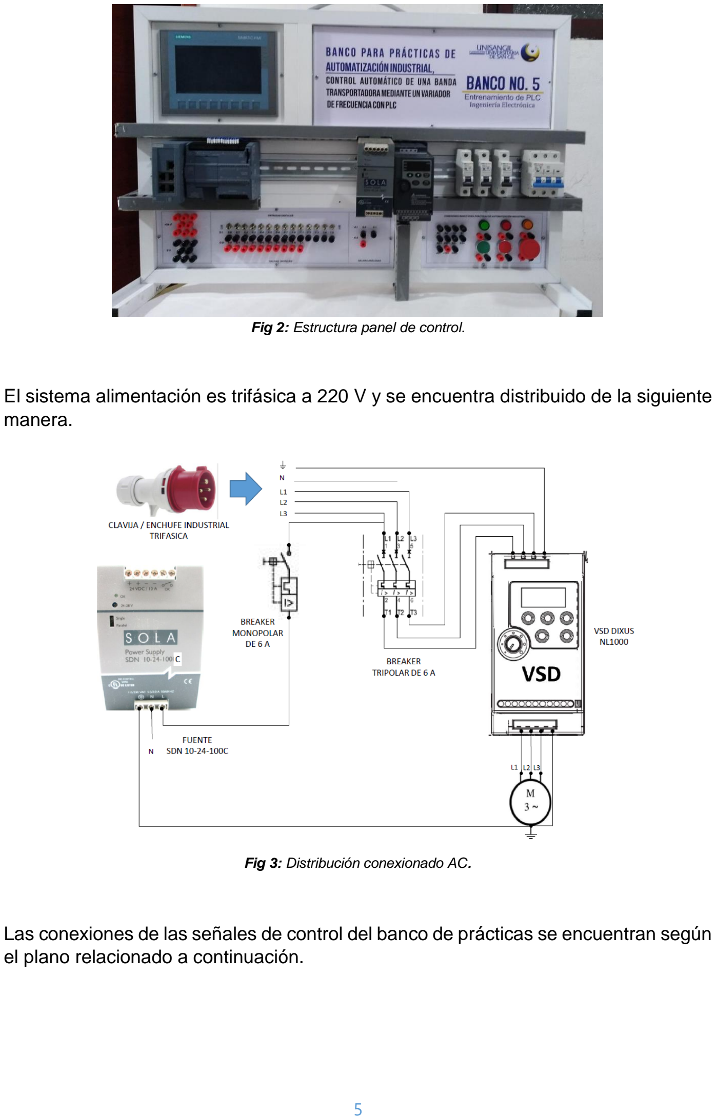
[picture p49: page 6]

Fig 2: Estructura panel de control.

El sistema alimentación es trifásica a 220 V y se encuentra distribuido de la siguiente manera.

Fig 3: Distribución conexionado AC.

Las conexiones de las señales de control del banco de prácticas se encuentran según el plano relacionado a continuación.

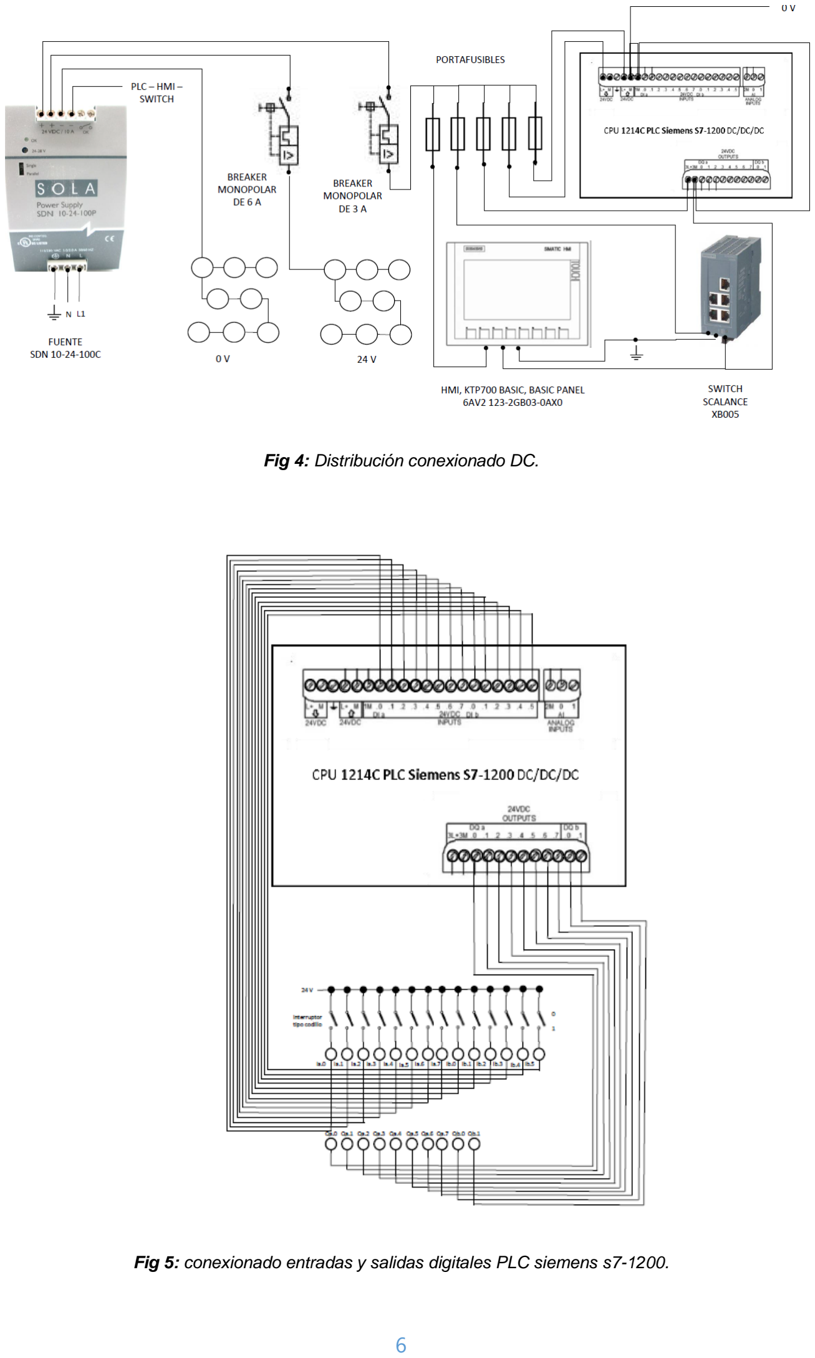
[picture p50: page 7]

Fig 4: Distribución conexionado DC.

Fig 5: conexionado entradas y salidas digitales PLC siemens s7-1200.

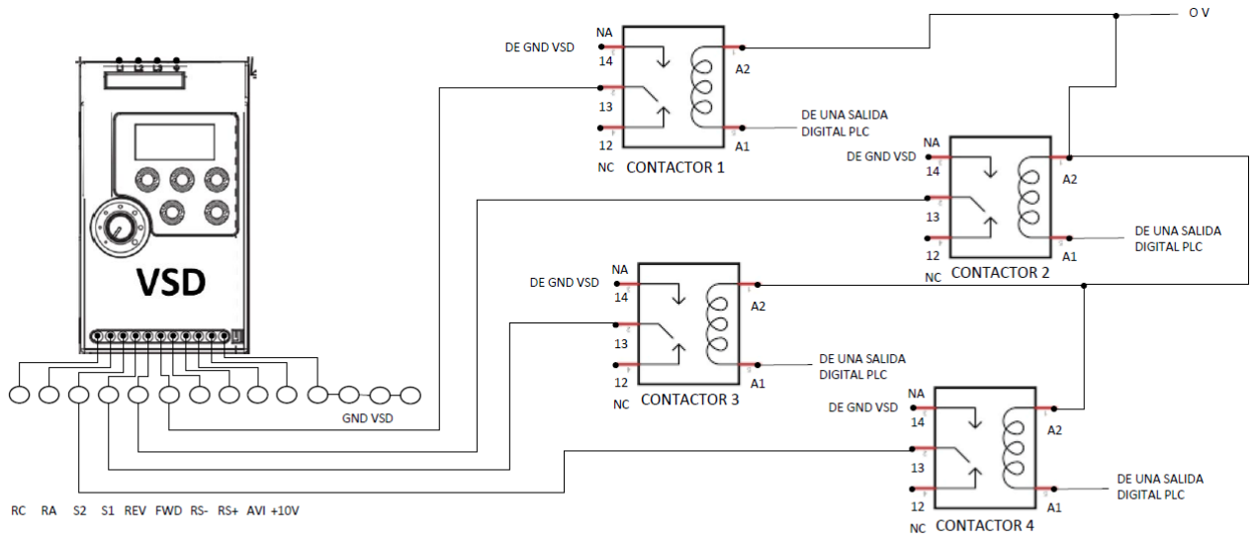
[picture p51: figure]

Fig 6: Conexionado borneras VFD y control por salidas digitales del PLC.

El variador de frecuencia tiene 4 entradas digitales las cuales pueden ser usadas según requerimiento, según el manual del VFD las señales de entrada se deben activar con pulsos de GND.

EL control automático de la banda transportadora se da por un PLC mediante el uso de un variador de frecuencia, este debe ser configurado según el manual de uso para los parámetros básicos; el programa para el PLC es desarrollado en TIA PORTAL, el cual controla el inicio, parada, cambio de giro y una parada de emergencia, todo comandado desde un controlador lógico programable (PLC). Que toma como entrada las señales de los pulsadores y entrega una señal de control para la operación del VFD.

SEGMENTOS DEL PROGRAMA

En este segmento 1: se realiza el enclavamiento principal de la variable “SISTEMA” la cual es accionada con el pulsador de color verde “START” permitiendo que la banda transportadora quede habilitada para su funcionamiento y en espera de una nueva orden para iniciar el desplazamiento a la derecha o la izquierda, a su vez encenderá la luz piloto color verde “LuzPilotoVerde”. Cuando se oprime el pulsador de color rojo “STOP” dejará de funcionar el SISTEMA. Por otra parte, al accionar el botón de parada de emergencia “EMERGENCYSTOP” también dejará de operar el sistema.

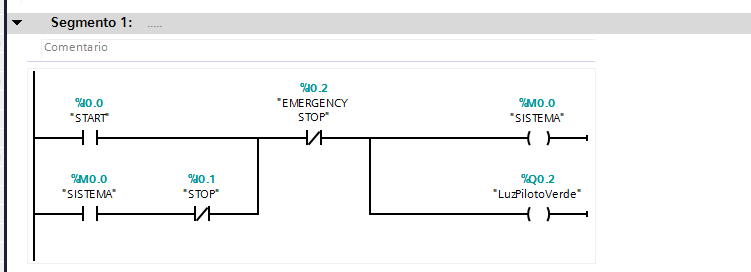
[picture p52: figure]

En este segmento 2: se realiza la configuración para el inicio del desplazamiento de la banda transportadora hacia el lado derecho. Una vez este habilitado el “SISTEMA” y después de ser accionado un pulsador “IFWD” conectado a la entrada digital %I0.3 se activará un pulso “FWD” que será conectado a la entrada digital del VFD permitiendo el giro de la banda transportadora hacia el lado derecho. También se garantiza que mientras no haya otro pulso solo girará hacia ese lado.

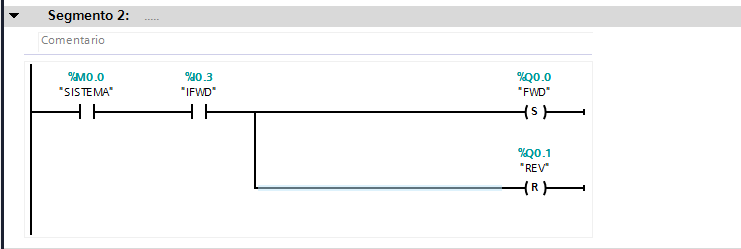
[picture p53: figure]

En este segmento 3: se realiza la configuración para el inicio del desplazamiento de la banda transportadora hacia el lado izquierdo. Una vez este habilitado el “SISTEMA” y después de ser accionado un pulsador “IREV” conectado a la entrada digital %I0.4 se activará un pulso “REV” que será conectado a la entrada digital del VFD permitiendo el giro de la banda transportadora hacia el lado izquierdo. También se garantiza que mientras no haya otro pulso solo girará hacia ese lado.

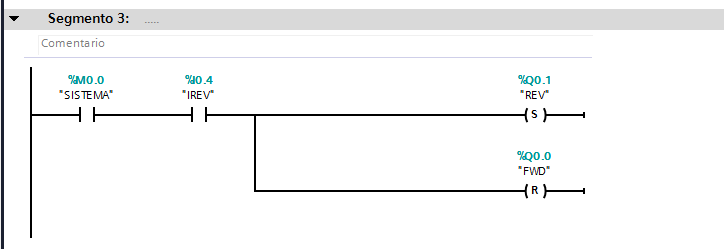
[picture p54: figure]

En este segmento 4: Se realiza la configuración para qué cuando esté desactivado el “SISTEMA” no se permita el desplazamiento de la banda para ninguno de los dos lados (derecha e izquierda). La desactivación se logra accionado el pulsador rojo “STOP” o el botón de para de emergencia “EMERGENCYSTOP”.

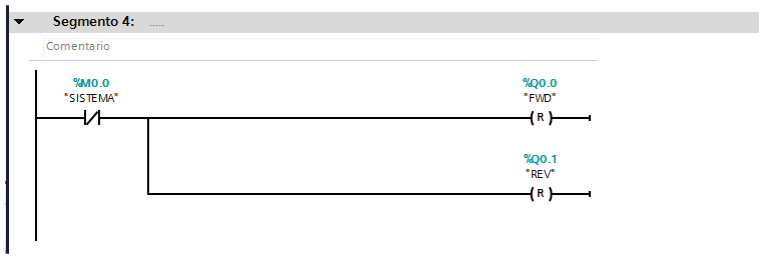
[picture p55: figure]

En este segmento 5: Se realiza la configuración para qué cuando se accione el pulsador rojo “STOP” se detenga la banda transportadora de manera segura con una desaceleración controlada y se encienda la luz piloto roja “LuzPilotoRoja” durante 5 segundos. Después de este tiempo se apagará la luz piloto roja.

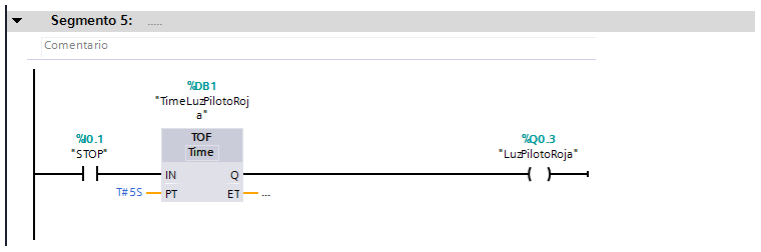
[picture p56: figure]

En este segmento 6: Se realiza la configuración para qué cuando se accione el botón de parada de emergencia “EMERGENCYSTOP” se detenga la banda transportadora de manera segura con una desaceleración controlada y se encienda la luz piloto roja “LuzPilotoNaranja” durante el tiempo que dure accionado el botón.

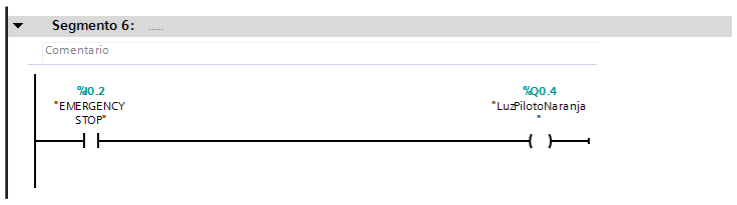
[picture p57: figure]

Adicionalmente, este banco para practicas cuenta con 4 guías de laboratorio, las cuales permite a los usuarios finales, interactuar con el sistema.

## FUNCIONAMIENTO

La banda transportadora cuenta con un sistema accionador de giro (motor trifásico de 0.4 HP y reductor de giro) este sistema es controlado por medio de un variador de frecuencia el cual debe ser configurado según el manual de usuario y acorde a las características y parámetros del motor descritos en la placa del mismo, con PLC el cual tiene un programa que controla automáticamente el arranque, parada, cambio de giro de la banda y parada por emergencia, desarrollado y ejecutado en TÍA PORTAL, los usuarios pueden validar el funcionamiento del sistema siguiendo el manual de uso, así como también puede interactuar variando las configuraciones básicas del VFD, así como también el programa del control automático.

Se recomiendo tener en cuenta la ingeniería inicial de construcción del banco, si se realiza modificaciones en la configuración y programación del proyecto, asegurarse de dejarlos según diseños o dado el caso y de ser necesario actualizar planos e información del proyecto.

CUIDADO MANTENEDOR.

Para la conservación y durabilidad del banco para prácticas, se le recomienda al usuario usarlo de manera responsable, respetando las indicaciones de las fichas técnicas de cada componente las cuales podrán ser consultadas en https://github.com/wilescruco/PDG2.git / ANEXOS / FICHAS TÉCNICAS.

Tener precaución al desconectar señales de control o potencia, asegurarse de marcar y conectar debidamente, según los planos anexos.

La pantalla HMI debe manipularse cuidadosamente con las manos limpias, igual que cualquier componente.

Asegurarse de dejar des alimentado y debidamente apagado el sistema luego de finalizar su uso.

No cortar cables ni modificaciones si contar con autorización para hacerlo, de ser así asegurarse de realizar las actualizaciones en los documentos técnicos

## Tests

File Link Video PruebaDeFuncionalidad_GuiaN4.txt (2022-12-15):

https://drive.google.com/file/d/1Vv3oh4V-yXtCipiyf5hOqXKAayLl0SHc/view?usp=sharing

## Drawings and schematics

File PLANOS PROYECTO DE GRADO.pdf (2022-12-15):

# PLANOS DE DISTRIBUCIÓN ELÉCTRICA AC, DC Y SEÑALES DE CONTROL

DEL BANCO PARA PRÁCTICAS DE AUTOMATIZACIÓN INDUSTRIAL,

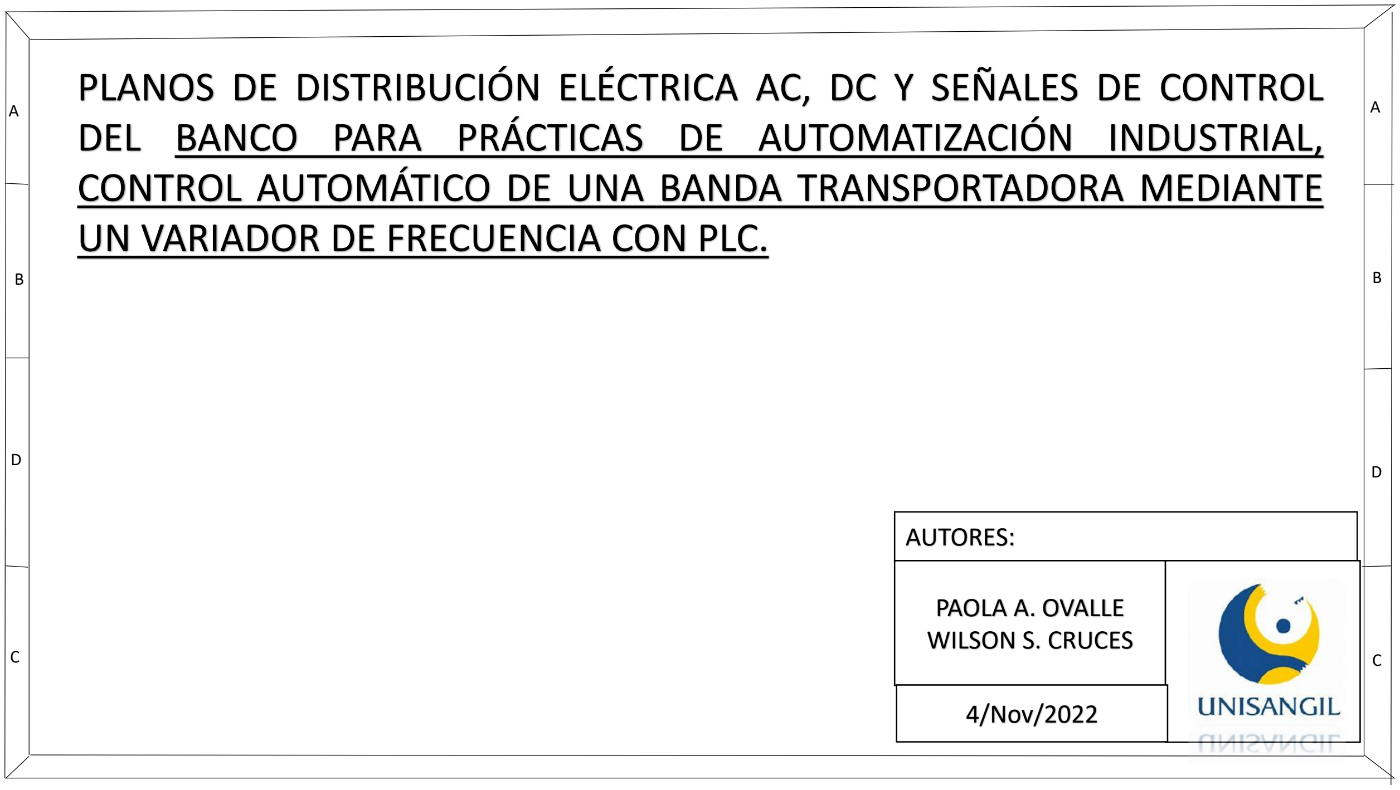
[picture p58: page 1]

A | A
B | B

D
D
C | C

# CONTROL AUTOMÁTICO DE UNA BANDA TRANSPORTADORA MEDIANTE

UN VARIADOR DE FRECUENCIA CON PLC.

## AUTORES:

## PAOLA A. OVALLE WILSON S. CRUCES

## 4/Nov/2022

## CONEXIONADO AC

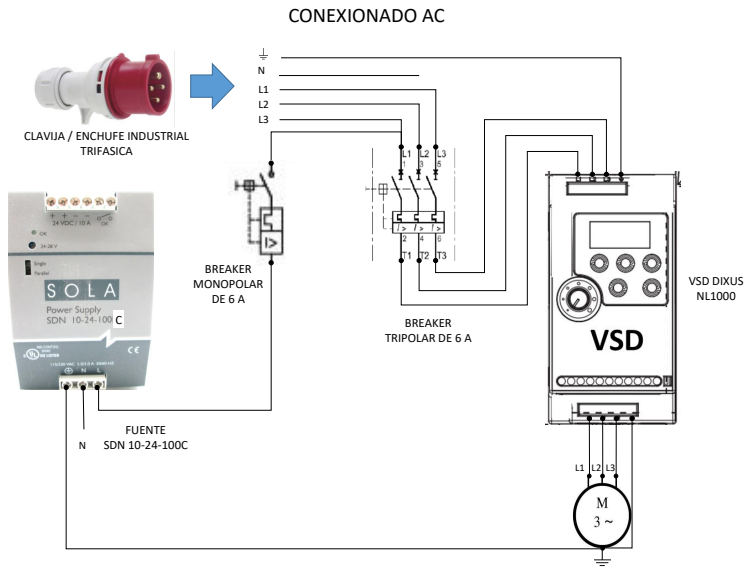
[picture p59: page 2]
BREAKER TRIPOLAR DE 6 A; BREAKER MONOPOLAR DE 6 A; VSD DIXUS NL1000; FUENTE SDN 10-24-100C; TRIFASICA

CLAVIJA / ENCHUFE INDUSTRIAL

## CONEXIONADO DC

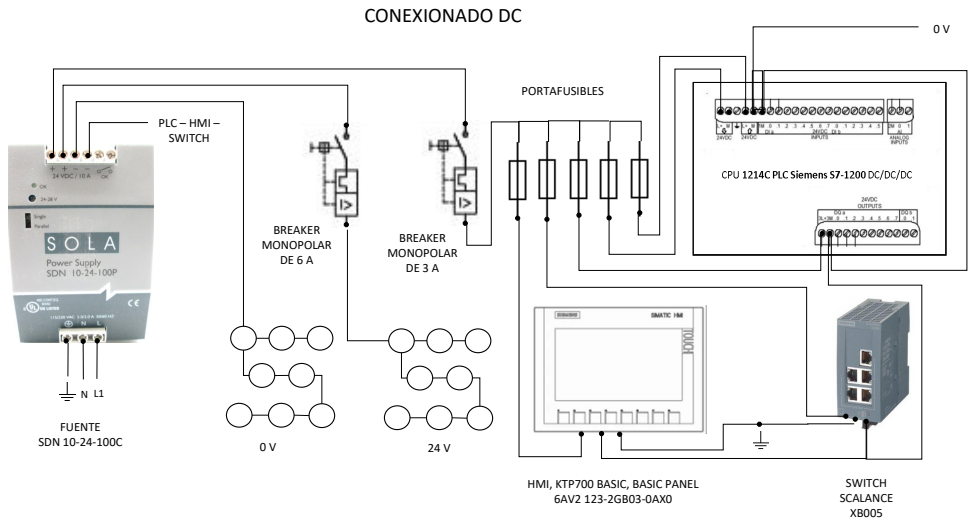
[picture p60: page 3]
BREAKER MONOPOLAR DE 6 A; FUENTE SDN 10-24-100C; BREAKER MONOPOLAR DE 3 A; PLC – HMI – SWITCH; SWITCH SCALANCE XB005; PORTAFUSIBLES

HMI, KTP700 BASIC, BASIC PANEL

## CONEXIONADO ENTRADAS Y SALIDAS DIGITALES PLC SIEMENS S7-1200

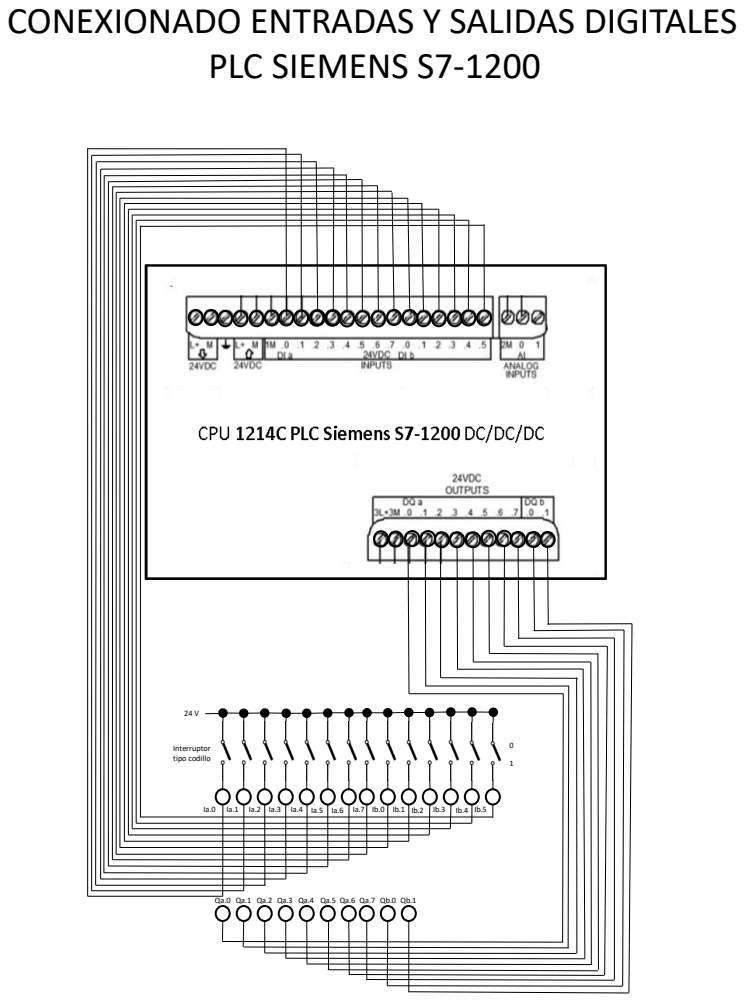
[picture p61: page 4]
Interruptor tipo codillo

## CONEXIONADO BORNERAS VSD Y CONTROL POR SALIDAS DIGITALES DEL PLC

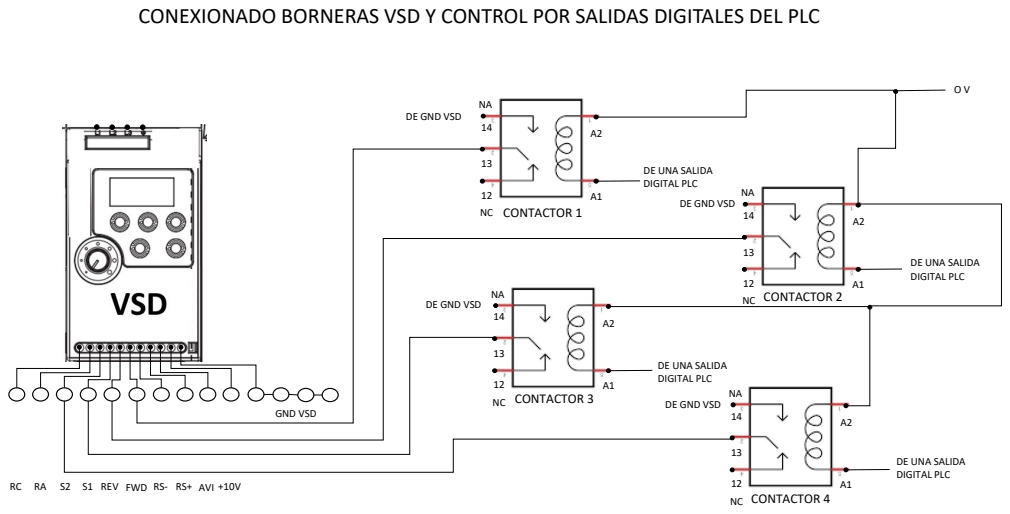
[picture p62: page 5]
S2 S1 REV FWD RS- RS+ AVI +10V; CONTACTOR 1; CONTACTOR 2; CONTACTOR 3; CONTACTOR 4

DE GND VSD

DE UNA SALIDA
DIGITAL PLC

DE UNA SALIDA DIGITAL PLC NA

GND VSD

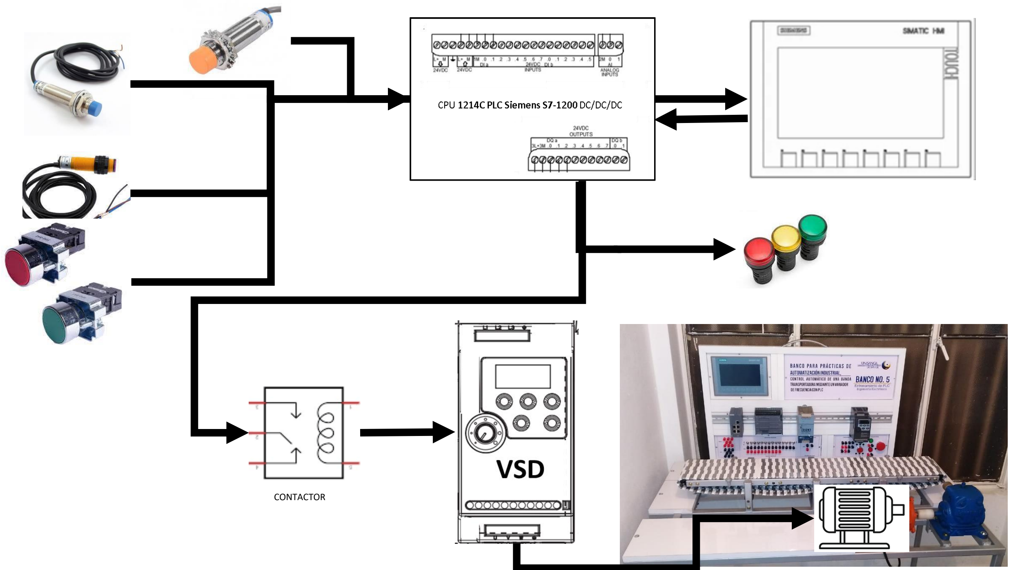
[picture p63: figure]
CONTACTOR

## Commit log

2022-05-27 Archivos y ANEXOS PDG
    [Acople Motoreductor.stl, Acople Reductor.stl, Engranaje.stl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]
2022-05-31 Envío de documentos correspondiente al 80%
2022-12-15 Documentación final
    [Acople Motoreductor.stl, Acople Reductor.stl, Engranaje.stl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]
